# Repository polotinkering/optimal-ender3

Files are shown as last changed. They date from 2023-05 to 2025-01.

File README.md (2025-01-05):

# optimal-ender3
**the best ender 3 setup in my opinion !**
---
so here it is ! It's time to share the current setup of my printer . 
I think that i am currently running one of the best budget setup for an ender 3.
I have done these modification by necessity or some just for aesthetic but always on a budget (No micro swiss here^^)
---
So let's start :
I have organized my mods by letters :
- [1] :best mods practicaly essential in my opinion
- [2] :very useful
- [3] :usefull
- [4] :not essential (aesthetic mods)
---
**so here it is in all his glory:**
1684315006498 (1)

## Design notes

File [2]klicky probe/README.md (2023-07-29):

i have recently integrated the kevinakasam klack ender probe 

it's a very good adition to the solid silicon plots since it correct the warping of the bed and it's very cheap:  

you only need 6 magnets 4 screws and a microswitch .  

I will not do the complete guide here but if you want to try it here is the [klack ender github](https://github.com/kevinakasam/KlackEnder-Probe)


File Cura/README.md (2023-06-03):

This is my go to cura plofile for classic PLA print 
---
I also share the profile i use to print the parts of my future Voron V2.4 . (all voron recomanded settings)

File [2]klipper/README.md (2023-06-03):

Klipper
---
What an interesting modification !  
some will be surprised that i don't put it on [S] tier but i feel like you can have some really good results with the classic marlin firmware .
I want to adress a big thanks to [JSTECH](https://www.youtube.com/@Jstech3d) and all of his discord for the support and the help while setting up klipper .  
So I have used a raspberry pi 2b with the [fluidd](https://docs.fluidd.xyz/) interface .
I have struggle a lot during the setup of the wifi dongle so i share my mistakes to avoid you hours of troubleshooting:
- 1 wrong usb dongle .I was trying a 5v TP-link wifi dongle and the rapi only supply 3v .[here](https://elinux.org/RPi_USB_Wi-Fi_Adapters) is the list of compatibles dongles .
- 2 I was using a fluidd pi image instead of a classic os and it is not compatibles with external usb .[This video](https://www.youtube.com/watch?v=oM2kAnITNyE&t=190s) can be usefull for wifi setup.

So i went with a raspbian lite image that i have flashed through the [raspberry pi imager](https://www.raspberrypi.com/software/)on my sd card.  
After this I have put the sd card in the pi and connected it via SSH with [putty](https://www.putty.org/)
Now you can follow the [kiauh documentation](https://github.com/th33xitus/kiauh)it simply consist on pasting commands on the console .
you need to install :
- klipper 
- moonraker
- a web interface : mainsail or fluidd *I have choose fluidd*  

After you need a "printer.cfg" file i have shared mine in the files section of this folder .  

this is my interface:
fluidd

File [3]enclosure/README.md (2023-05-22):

simple ikea lack enclosure 
---
I have done it because im plannin gon building a voron andd for the voron i need a ABS capable machine .  
It's also very convinient because you can put things on top of the enclosure to keep more space on the desk .

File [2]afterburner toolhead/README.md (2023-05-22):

Voron afterbuner
---
one of the best upgrades i have done until now
this is why you would want to switch to afterbuner :
- print easily flexibles materials like TPU .
- do maintenance much more easily because it is very convenient to dissassemble .
- swap from one hot end to another realy quickly .
- have a much more slylish printer 😎.

I have reused the gear from my dual gear extruder seen above.  
it have worked perfectly great since the biggining and after swapping to a mosquito knock off i don't have any trouble when printing hight temp material like ABS or PETG.
And if you have a voron you can have a common stock of spare printed parts wich is realy convinient if you have a problem on one of your printers .  
Big thanks to the voron team for developping this toolhead !  
for this upgrade you will need :
- A [screw kit](https://fr.aliexpress.com/item/1005003998948585.html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) for afterburner because it's so much simple and not more expensive than self source all screw. aprox 10€
- 2040 24V [blower fan](https://fr.aliexpress.com/item/1005003879817745.html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) for about 4€.
- [dual gear kit](https://fr.aliexpress.com/item/1005005061611663.html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) (i have reused the one from my bond tech knock off)
- A [thiner stepper](https://fr.aliexpress.com/item/1005003226027617.html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) .15€  
Make sure to check the assembly manual before printing every thing .

Polish_20230518_120700527

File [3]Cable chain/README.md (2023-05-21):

Simple cable chain for the bed
it requiered :
- the printed parts 
- 2 or 4 zip ties


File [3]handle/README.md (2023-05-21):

Just a handle for easy carrying .
---
Print it pretty strong :
- 3 perimeters
- 20% infill or more
- 4 top/bottom  
files are from [this guy](https://www.thingiverse.com/guppyk/designs)


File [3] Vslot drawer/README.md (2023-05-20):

This is a simple 3d printed drawer for the included tools .  
You need:
- the printed part from [this guy](https://www.thingiverse.com/edison13/designs)
you can print it with your normal print setting with any filament .

drawer

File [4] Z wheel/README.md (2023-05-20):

this is a simple Z whell to move the Z axis easely.  
not that usefull but kinda cool !
---
it requiered :
- one printed part .from [this guy](https://www.thingiverse.com/s_vayner/designs)  
 


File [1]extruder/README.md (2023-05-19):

So first mod i have done to my ender 3 about 1 week after building the printer was changing the crappy plasticky extruder to a dual gear bondteck knock off :
---
this mod will cost you :
- about 15€ for [this very cheap knock off](https://fr.aliexpress.com/item/1005003423850142.html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)
- 30€ for [this good quality clone](https://fr.aliexpress.com/item/1005003092239261.html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)
- aproximately 100€ for [the original bontech](https://www.3djake.fr/bondtech/extruder-bmg-droit) depending from were you order

this mod is verry usefull and it will last you longer than the plastic one .
extrudr
*sorry for the bad photo quality i don't take photo of my printer too often*  

optionaly you can also like me upgrade later on the voron afterburner. *explenation on the afterbuner category*

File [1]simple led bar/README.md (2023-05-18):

This mod is pretty simple but in my opinion very usefull and it consist on a simple led strim on a holder in the top V slot .  
for this upgrade you will need:
- a simple [5v led strip](https://fr.aliexpress.com/item/1005003256544536.html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) it's 3€ for 1 meter (i power it from the bl touch port)*note:you can also power it from the psu with 24V leds*
- the 3 printed parts on the "STL" folder wich are from [this guys](https://www.thingiverse.com/smokyjoe/designs) (thanks to him) *note :you should print LED_Profile_V2.stl X2*
- some wire
- [A switch](https://fr.aliexpress.com/item/32822549892.html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) for around 3€ you can get 10 (I have choose a simple round one to make integration easier)
- maybe a connector if you want a clean instalation .


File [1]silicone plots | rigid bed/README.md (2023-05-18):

Silicon bed springs
---
In this page i will cover a very simple yet very usefull mod that i have done on day one :
these silicone plots instead of the original bed springs.  
It makes the bed a lot more rigid and don't require a lot of time and money so it's a must have on any I3 type of printer !
necessary parts :
- it will cost you around 4€ for [the kit of 4](https://fr.aliexpress.com/item/1005001823789355.html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) and are very durable


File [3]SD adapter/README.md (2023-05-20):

SD slot instead of micro SD
---
it's simple : micro sd is trash .  
It can't last very long ,it requiered more adapter to plug into your computer .
---
for this mod you will need :
- A [micro SD to SD adapter](https://fr.aliexpress.com/item/1005003299104936.html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) for about 3€ *make sure to select "TF-SD"*
- 2 printed parts
Polish_20230518_190414510
thanks to [Scott Yu-Jan](https://www.youtube.com/@ScottYuJan) for this remix and his videos

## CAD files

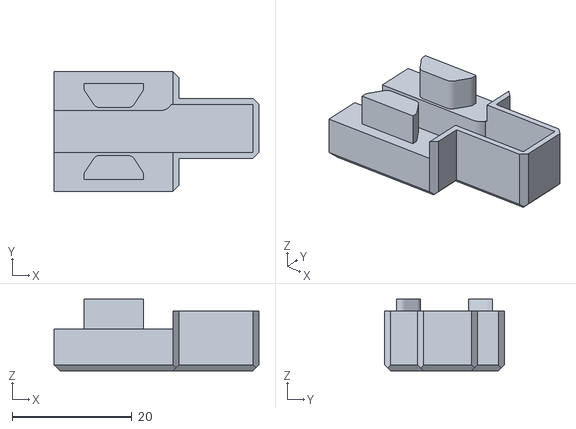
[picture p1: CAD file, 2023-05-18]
[1]simple led bar/STL/V2_V3_Endcap_left.stl
34.3 x 20.0 x 12.0

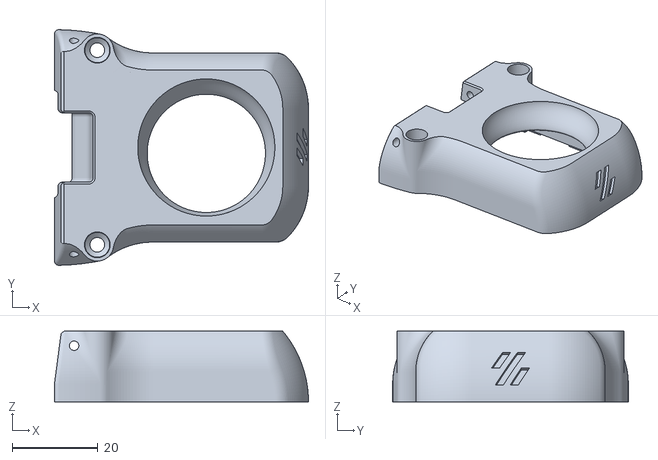
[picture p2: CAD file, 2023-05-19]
[2]afterburner toolhead/STL/Afterburner/[a]_blower_housing_front.stl
59.3 x 55.0 x 16.5

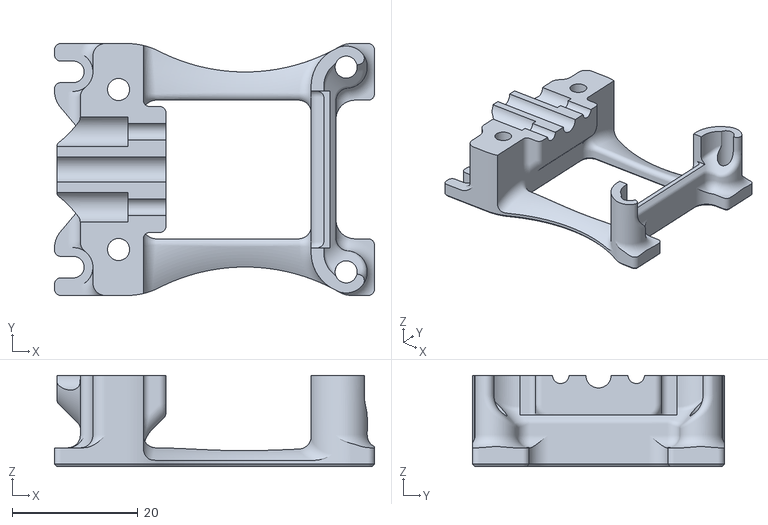
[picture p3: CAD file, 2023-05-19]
[2]afterburner toolhead/STL/toolcartridges/mosquito/printhead_rear_mosquito.stl
50.8 x 40.0 x 14.5

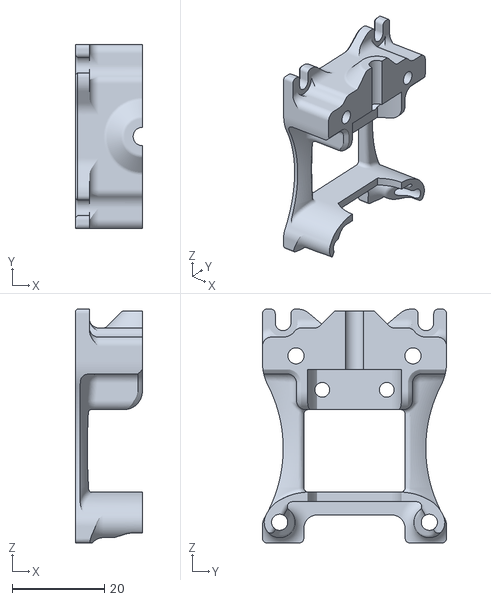
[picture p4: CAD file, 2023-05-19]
[2]afterburner toolhead/STL/toolcartridges/stock MK8/AB_Mk8_Ender5_stock_Back.stl
14.5 x 40.0 x 50.8

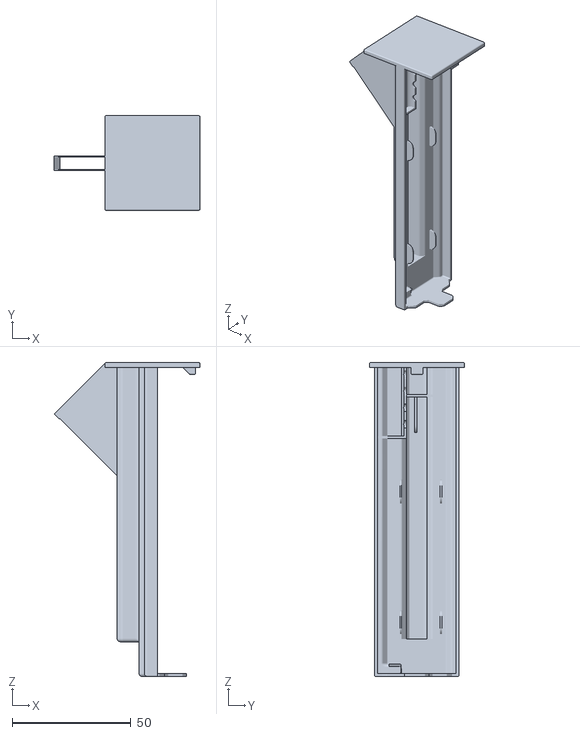
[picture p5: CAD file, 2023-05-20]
[3] Vslot drawer/STL/40x40AL_drawer_v3.STL
61.3 x 39.8 x 132.0

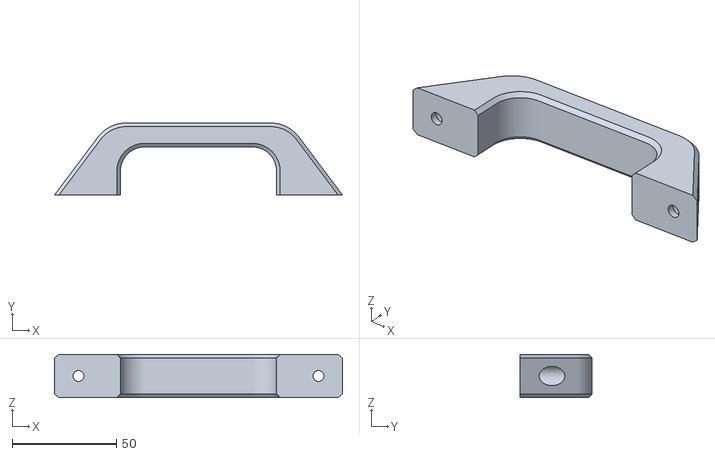
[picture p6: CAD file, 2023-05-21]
[3]handle/Handle_LARGE.stl
138.0 x 34.5 x 20.7

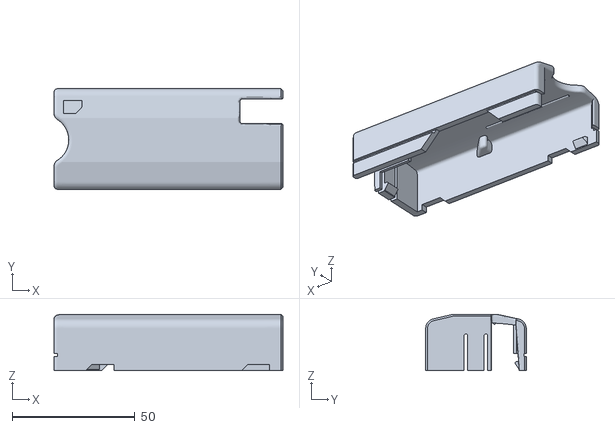
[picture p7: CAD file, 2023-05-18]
[3]SD adapter/STL/SD_Cover_remixed_updated_size.stl
93.4 x 41.0 x 23.0

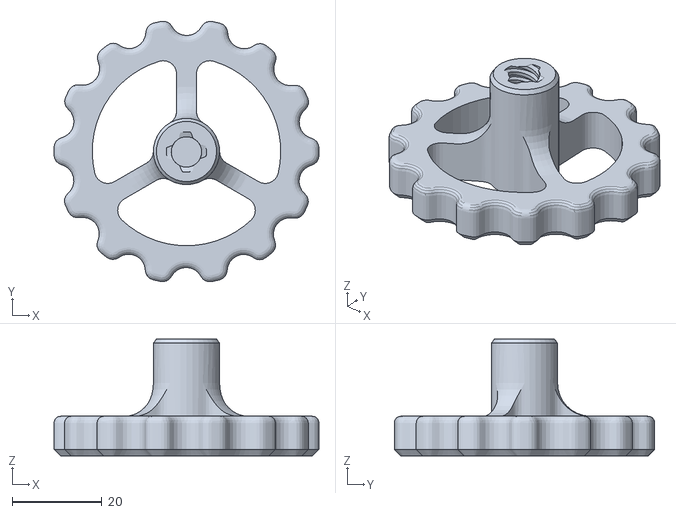
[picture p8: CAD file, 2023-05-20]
[4] Z wheel/STL/ZAxis_knob.stl
59.0 x 58.0 x 26.0

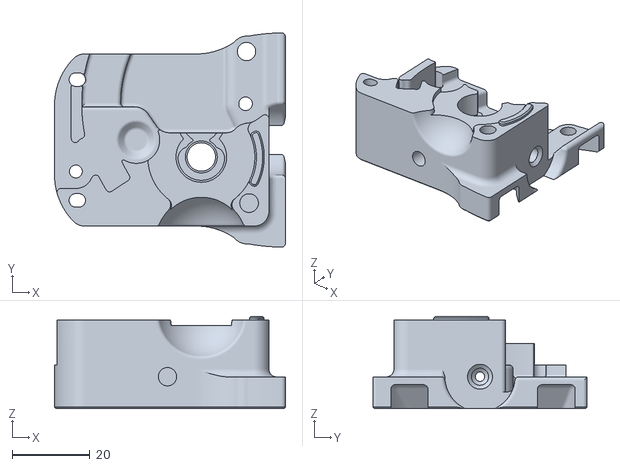
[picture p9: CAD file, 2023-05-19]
[2]afterburner toolhead/STL/Afterburner/extruder_body.stl
59.3 x 55.0 x 23.7

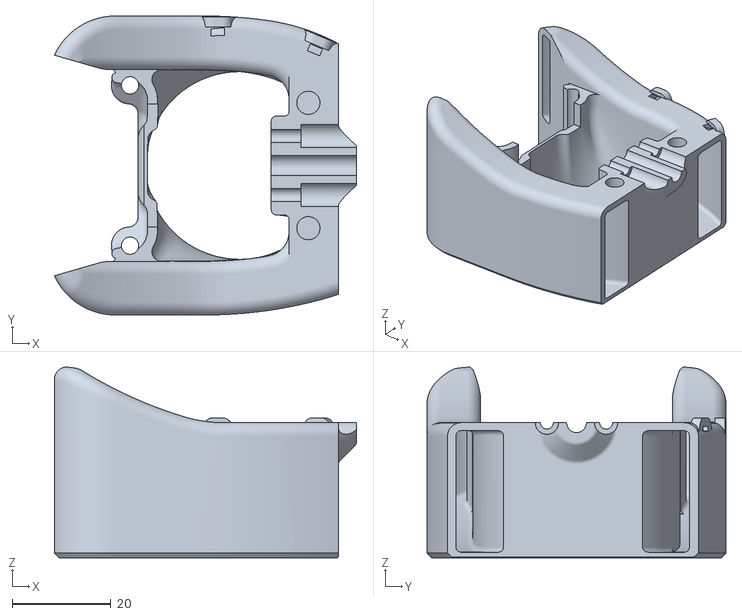
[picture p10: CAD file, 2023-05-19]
[2]afterburner toolhead/STL/toolcartridges/mosquito/printhead_front_mosquito.stl
61.2 x 60.6 x 38.7

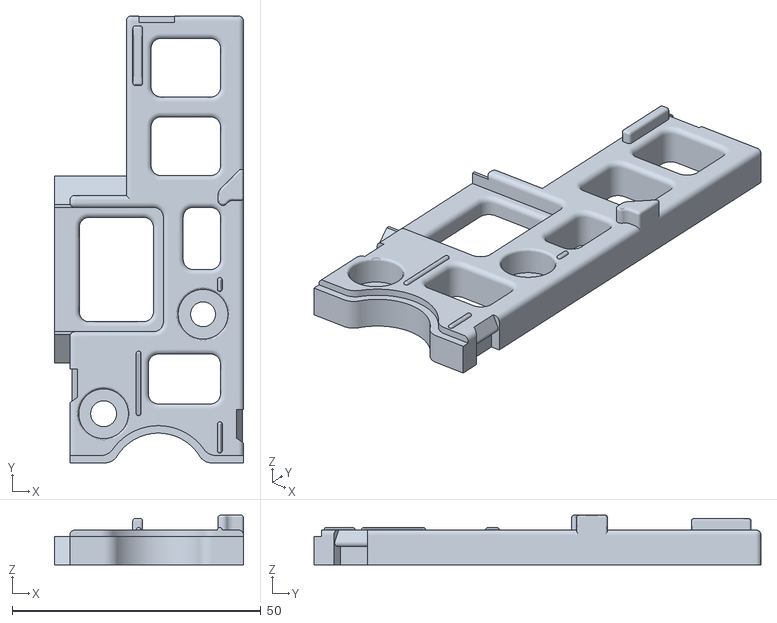
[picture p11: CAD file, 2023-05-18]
[3]SD adapter/STL/SD_base_plate .stl
38.0 x 89.9 x 10.00

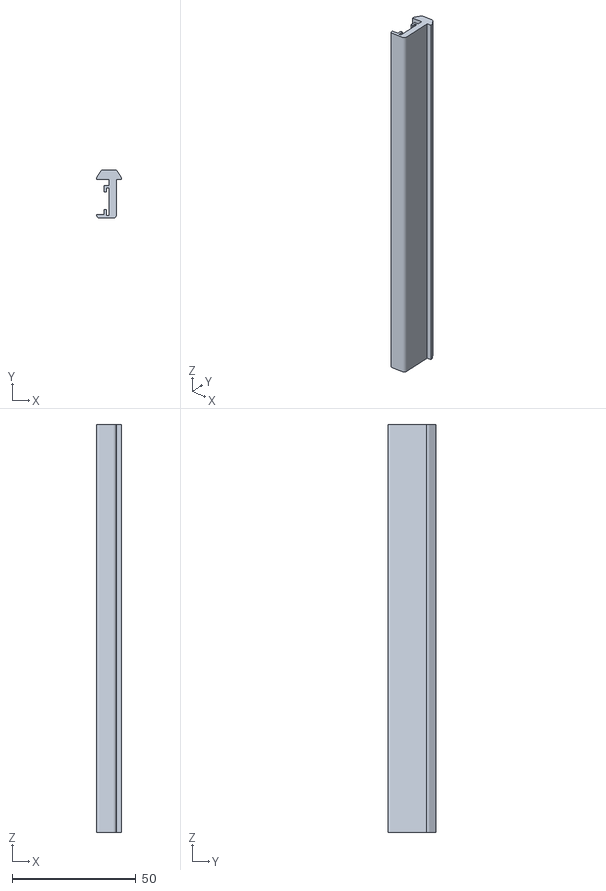
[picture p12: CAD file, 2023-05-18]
[1]simple led bar/STL/LED_Profile_V2.stl
10.0 x 19.6 x 165.0

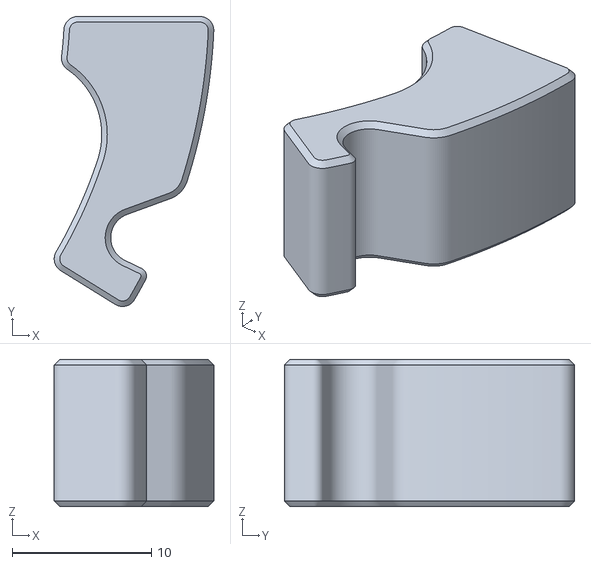
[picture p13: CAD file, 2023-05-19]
[2]afterburner toolhead/STL/Afterburner/[a]_latch_shuttle.stl
11.5 x 20.9 x 10.6

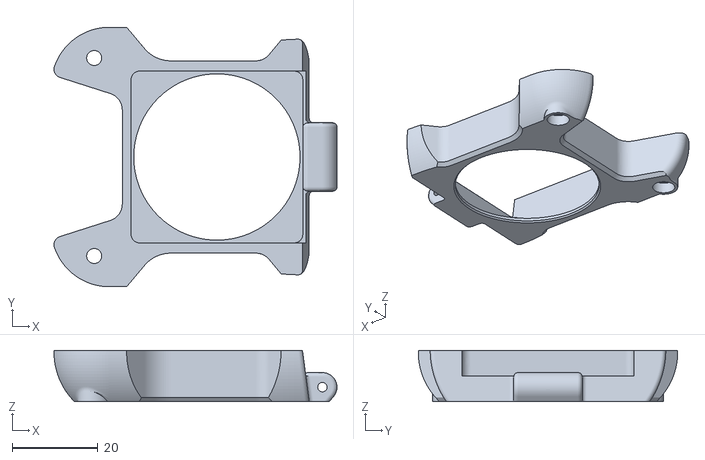
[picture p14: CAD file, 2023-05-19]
[2]afterburner toolhead/STL/Afterburner/hotend_fan_mount.stl
66.1 x 60.6 x 12.0

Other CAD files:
[1]simple led bar/STL/V2_V3_Endcap_right.stl
[2]afterburner toolhead/STL/Afterburner/[a]_latch.stl
[2]afterburner toolhead/STL/Afterburner/afterburner-motor-plate-ender3v2_BLT_updated.stl
[2]afterburner toolhead/STL/Afterburner/blower_housing_rear.stl
[2]afterburner toolhead/STL/Afterburner/[a]_guidler.stl

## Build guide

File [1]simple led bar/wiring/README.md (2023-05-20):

this is the wiring i used to power the leds :
---
wiring shema

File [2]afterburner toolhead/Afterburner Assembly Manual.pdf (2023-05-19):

1

# AFTERBURNER

### VORONDESIGN.COM

07-13-2021

2

CARRIAGE | VORONDESIGN.COM

M3x30 SHCS

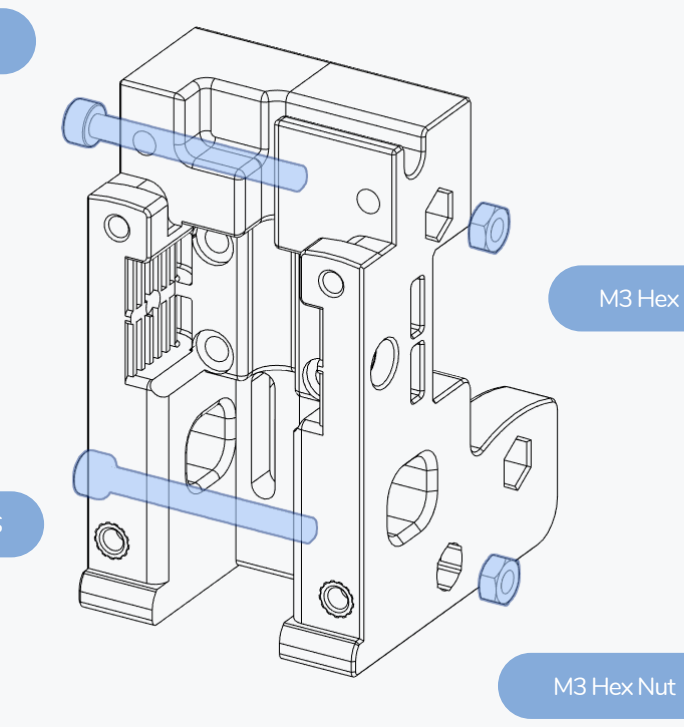
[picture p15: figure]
M3 Hex Nut

M3x30 SHCS

M3 Hex Nut

Heat Sets

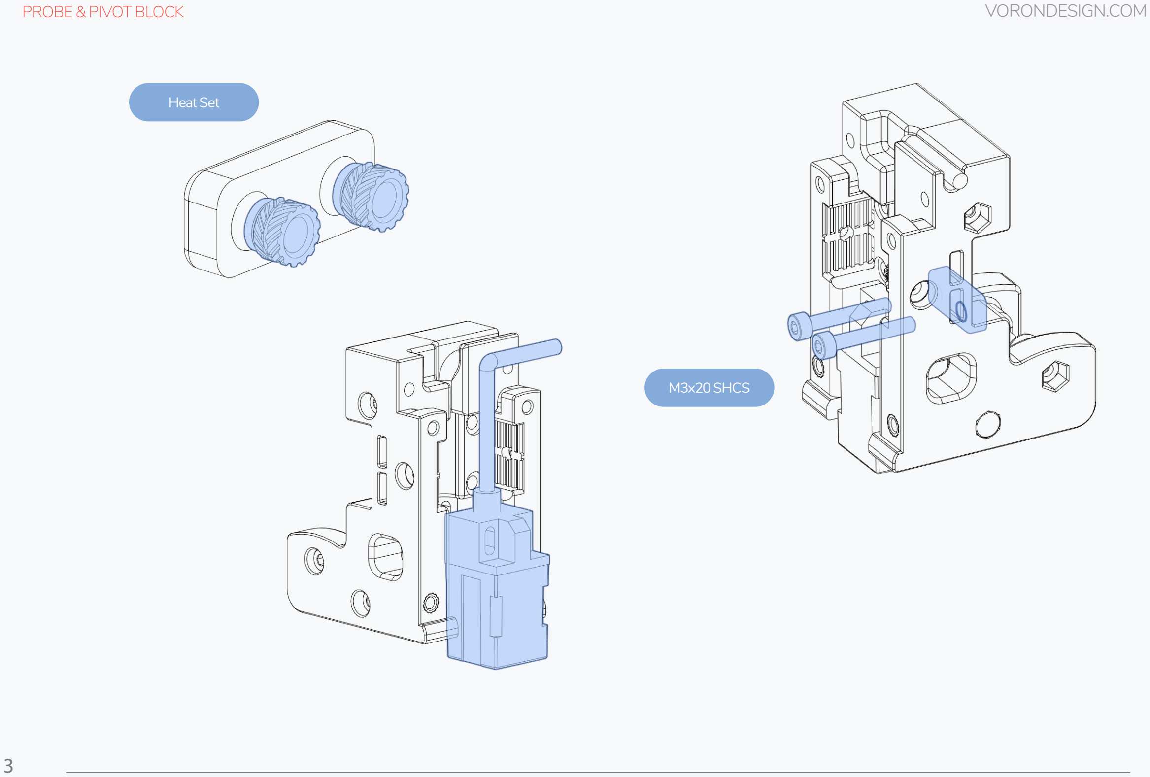
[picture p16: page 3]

3

PROBE & PIVOT BLOCK | VORONDESIGN.COM

Heat Set

M3x20 SHCS

4

XY BELT RETENTION | VORONDESIGN.COM

Heat Set

M3x12 SHCS

5

CARRIAGE MOUNTING | VORONDESIGN.COM

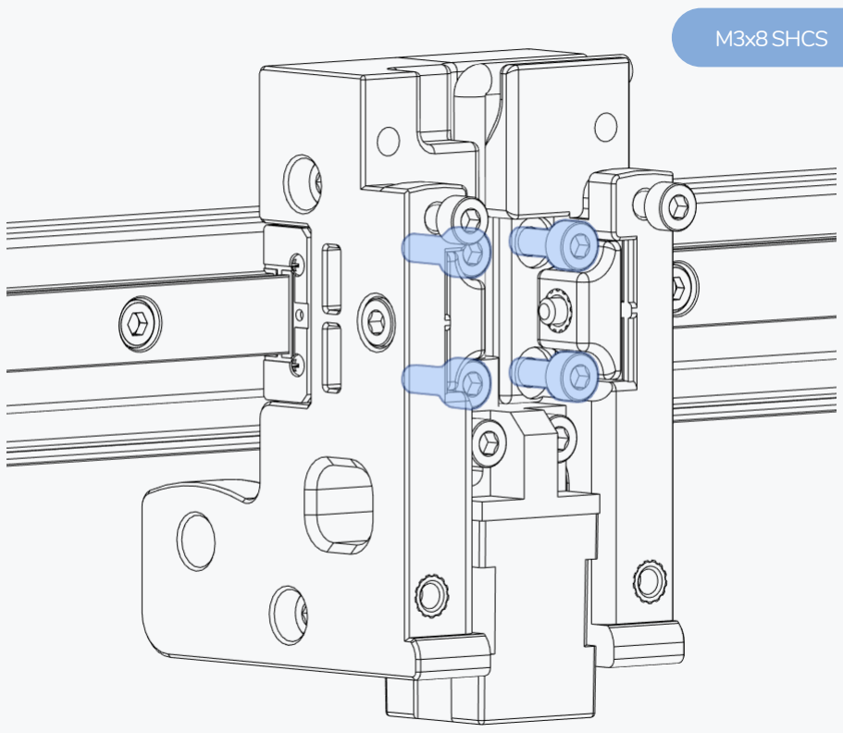
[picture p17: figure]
M3x8 SHCS

BUTTON HEAD OPTION
If you happen to have some M3x8 BHCS laying around
you can use those here. It can make belting the gantry in later steps a little easier but it’s not a big deal if you don’t have them.

PIVOT BLOCK | VORONDESIGN.COM

6

M3x8 SHCS
M3x30 SHCS

M3 Nut

DO NOT TIGHTEN (YET)
Leave these loose. You’ll need to aslign the rail before tightening. See discord if you need help with the correct procedure.

A BELT ROUTING | VORONDESIGN.COM

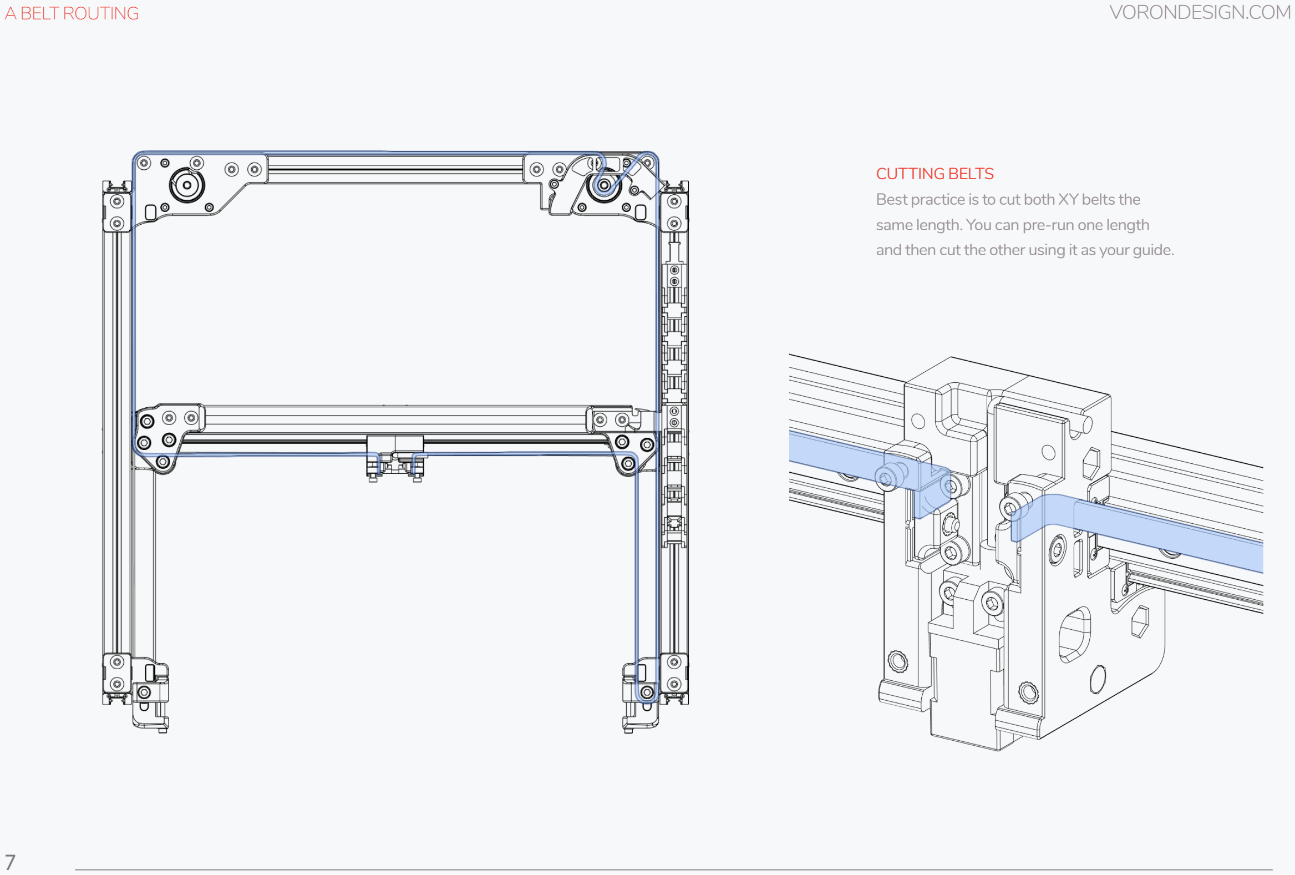
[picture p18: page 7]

7

CUTTING BELTS
Best practice is to cut both XY belts the same length. You can pre-run one length and then cut the other using it as your guide.

B BELT ROUTING | VORONDESIGN.COM

8

SECURING BELTS
Pick one side of the carriage and tighten the belts down flush with the front face. This allows you to pull the belts on the other side an equal length to help keep things square.

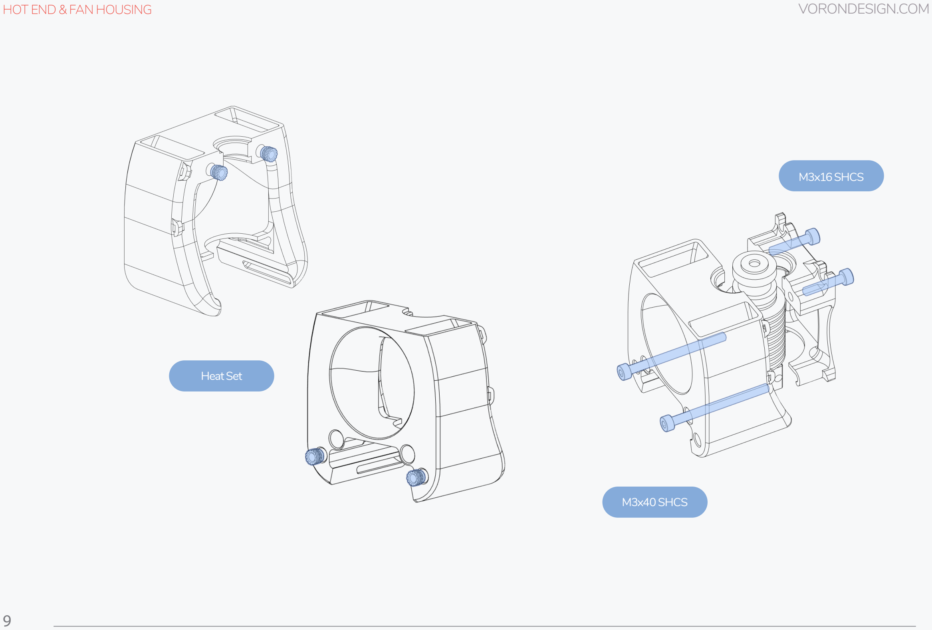
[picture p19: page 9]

9

HOT END & FAN HOUSING | VORONDESIGN.COM

Heat Set

M3x40 SHCS

M3x16 SHCS

10

HOT END RETENTION | VORONDESIGN.COM

M3x16 SHCS

TEST FIT HOUSING
Make sure to test fit the hot end housing. It should be able to slide in with firm pressure but not be loose enough that it can wobble.

11

CLOCKWORK HEAT SETS | VORONDESIGN.COM

INSTALL HEAT SET INSERTS
You will need to install heat set inserts into the locations shown on this page. Take note of the different cable chain mounts and use the one that best fits your build.

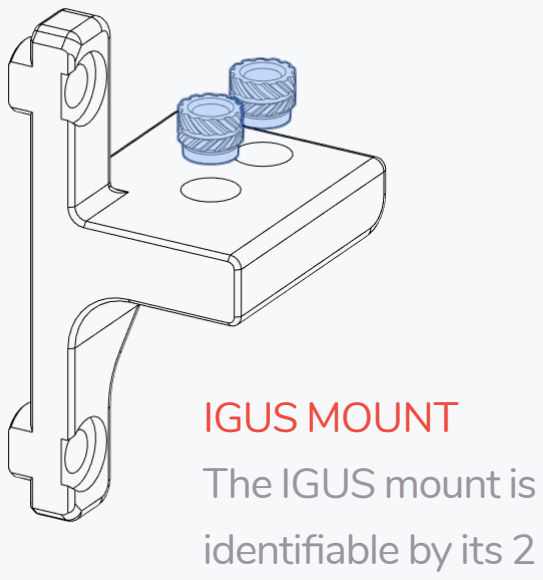
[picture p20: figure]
IGUS MOUNT The IGUS mount is identifiable by its 2
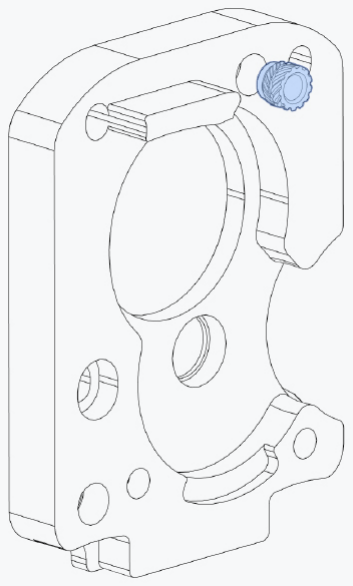
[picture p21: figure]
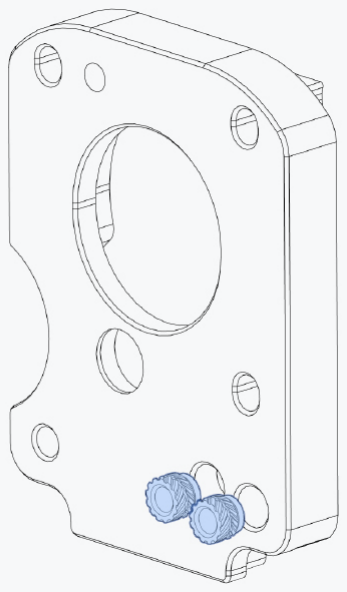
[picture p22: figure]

mounting holes.

is identifiable by its
3 mounting holes.

12

CLOCKWORK HEAT SETS CONT. | VORONDESIGN.COM

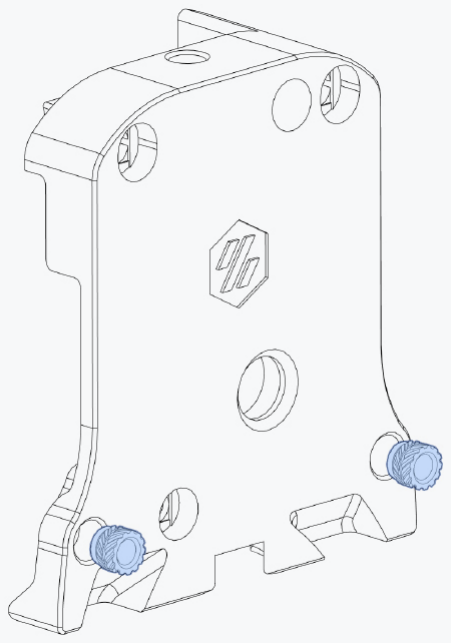
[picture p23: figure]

13

MOTOR PLATE | VORONDESIGN.COM

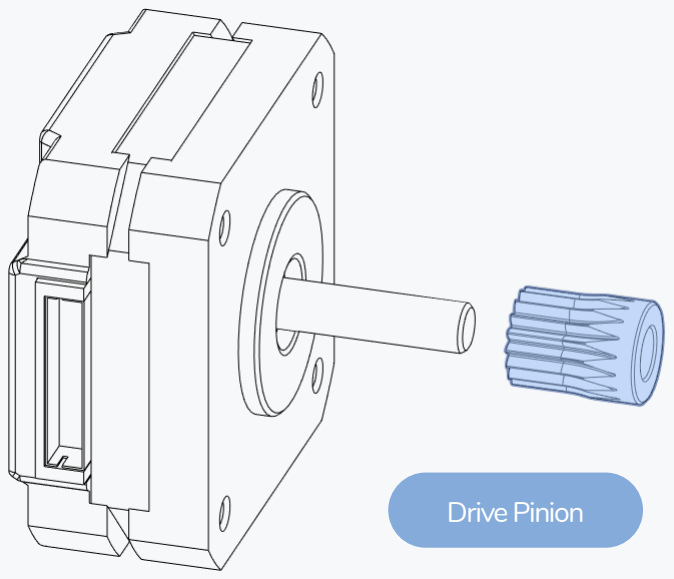
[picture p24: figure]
Drive Pinion
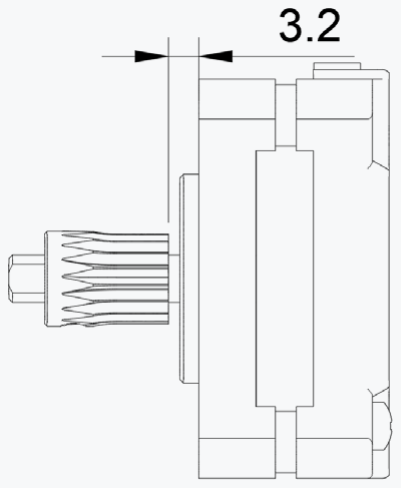
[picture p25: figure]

DRIVE PINION SPACING
Take care when installing the drive pinion on the extruder motor. It should be spaced 3.2mm from the main body of the stepper motor.

STEPPER MOTOR ORIENTATION
Make sure to orient the motor on the drive plate so that the wires are on the left side. This will allow correct routing through the cable cover that will be installed later.

14

MOTOR PLATE ALIGNMENT | VORONDESIGN.COM

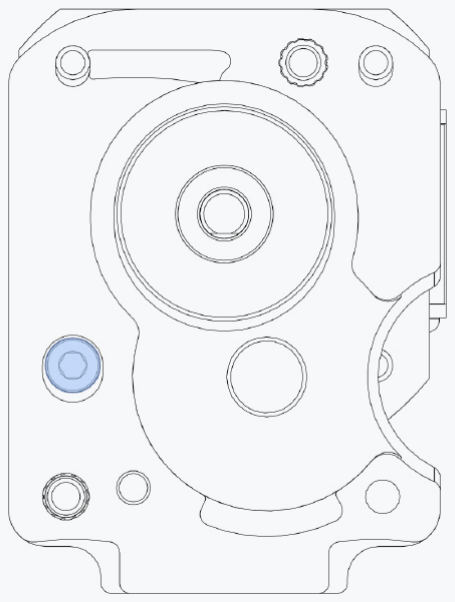
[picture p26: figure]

M3x8 SHCS

ADJUSTABLE MOTOR POSITION
The motor position is adjustable to allow for properly meshing of the drive gears.
We recommend you start in the top most position of the slot, but check Discord if you have questions on how to properly adjust this.

15

DRIVE GEAR | VORONDESIGN.COM

CHECK PLACEMENT
Ensure the filament drive gear is fully seated against the drive shaft gear.

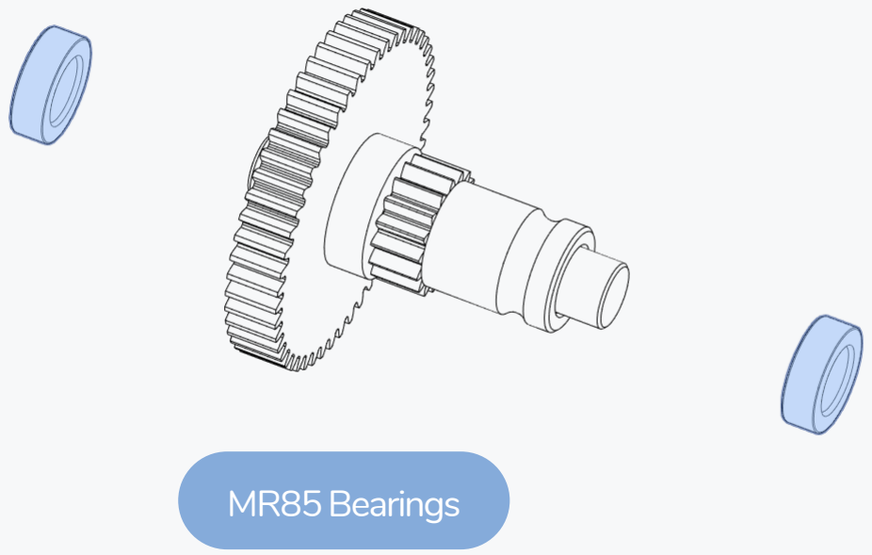
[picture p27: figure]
MR85 Bearings

BEARING FIT
The MR85 bearings should slip on to the drive shaft easily allowing the assembly to self center itself in relation to the filament.

If you find that they are too tight, you can lighty sand the drive shaft.

MAIN BODY | VORONDESIGN.COM

16

CHECK CLEARANCE
Make sure the drive shaft is not rubbing on the extruder motor. You can sand the face of the drive shaft if required.

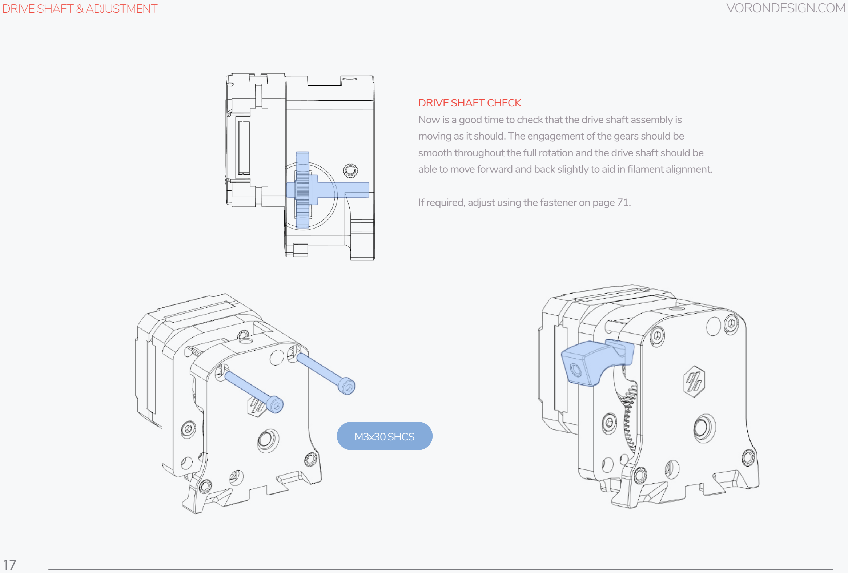
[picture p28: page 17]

17

DRIVE SHAFT & ADJUSTMENT | VORONDESIGN.COM

M3x30 SHCS

DRIVE SHAFT CHECK
Now is a good time to check that the drive shaft assembly is moving as it should. The engagement of the gears should be smooth throughout the full rotation and the drive shaft should be able to move forward and back slightly to aid in filament alignment.

If required, adjust using the fastener on page 71.

18

IDLER ASSEMBLY | VORONDESIGN.COM

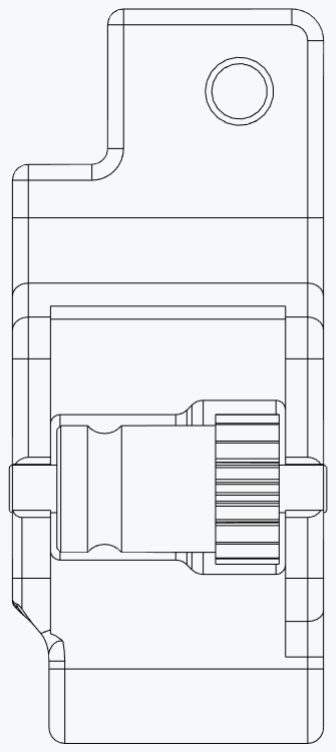
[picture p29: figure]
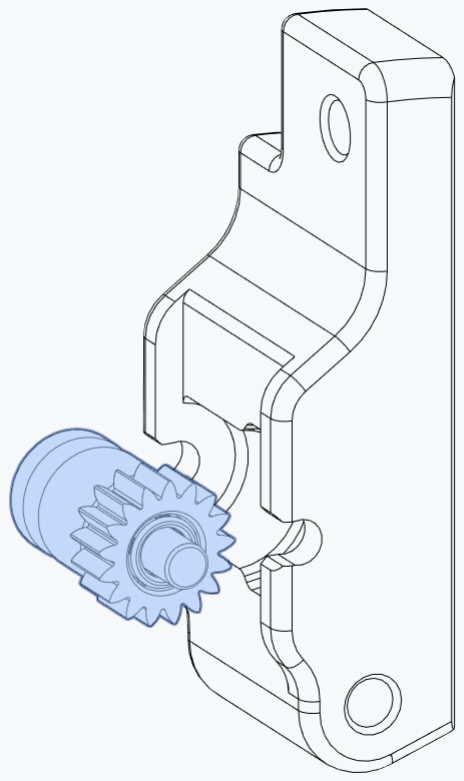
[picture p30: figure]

LUBRICATION
The idler assembly requires lubrication to ensure smooth operation and longevity. Refer to the BOM for lubricant options.

19

GUIDLER | VORONDESIGN.COM

M3x30 SHCS

20

LATCH INSTALL | VORONDESIGN.COM

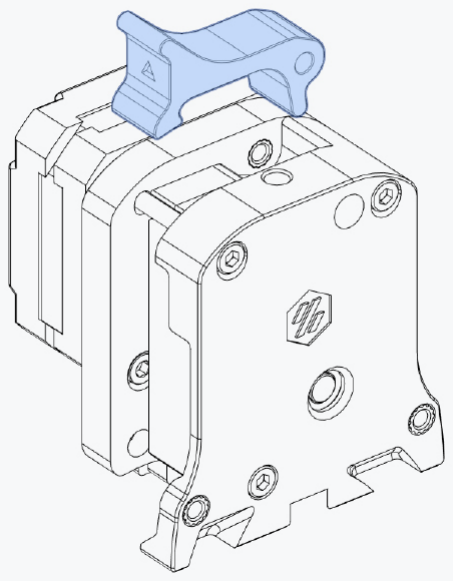
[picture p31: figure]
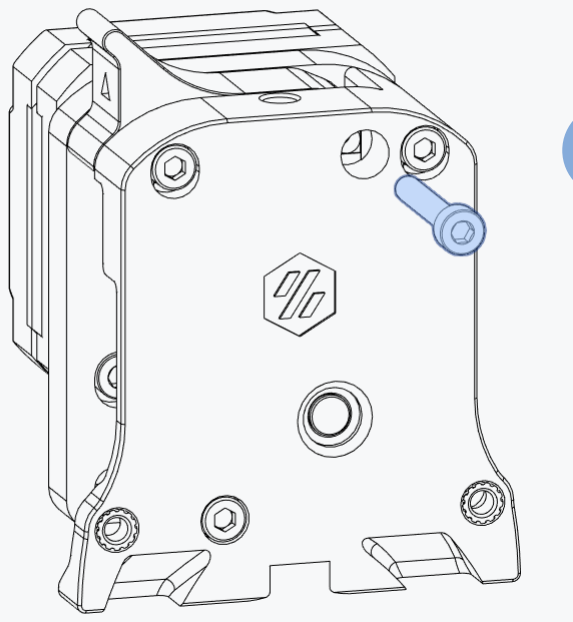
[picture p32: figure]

M3x20 SHCS

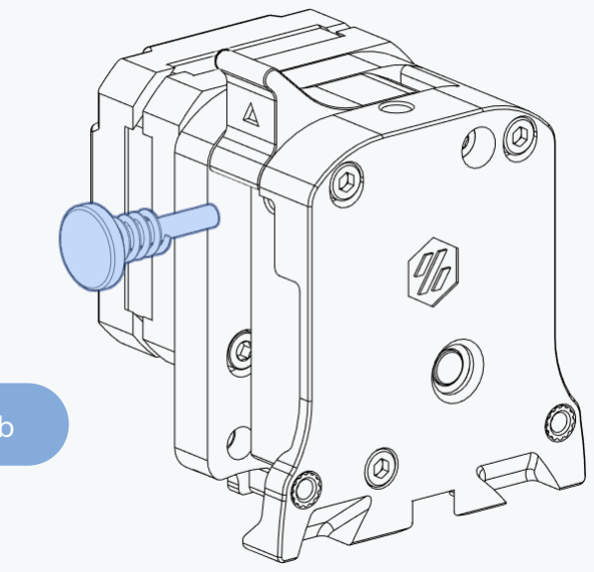
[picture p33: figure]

Tension Knob

21

CHAIN MOUNT | VORONDESIGN.COM

REMOVE SCREWS
Carefully remove the two screws on the left side of the extruder motor. We are going to be replacing these in further steps.

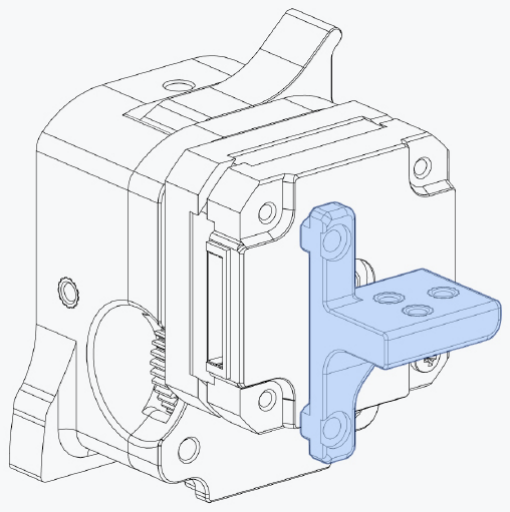
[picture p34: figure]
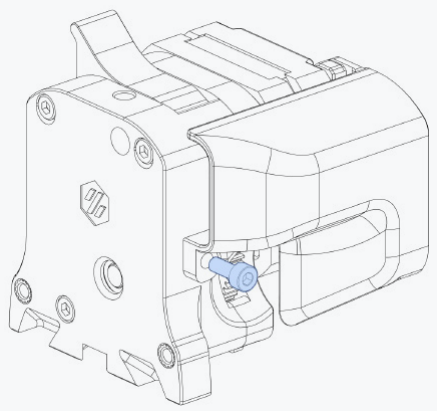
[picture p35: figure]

CABLE COVER | VORONDESIGN.COM

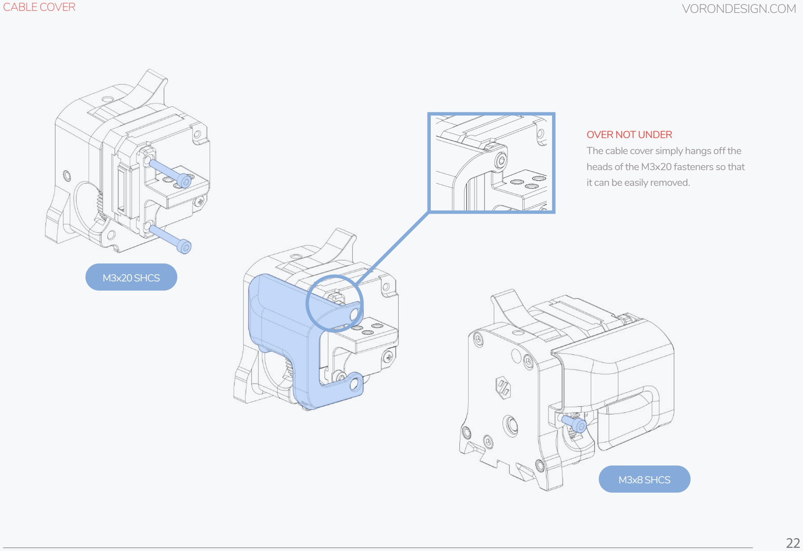
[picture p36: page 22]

22

M3x20 SHCS

M3x8 SHCS

OVER NOT UNDER
The cable cover simply hangs off the heads of the M3x20 fasteners so that it can be easily removed.

23

CLOCKWORK MOUNTING | VORONDESIGN.COM

M3x30 SHCS

M3x16 SHCS

M3x20 SHCS

M3x30 SHCS

HOT END INSTALL | VORONDESIGN.COM

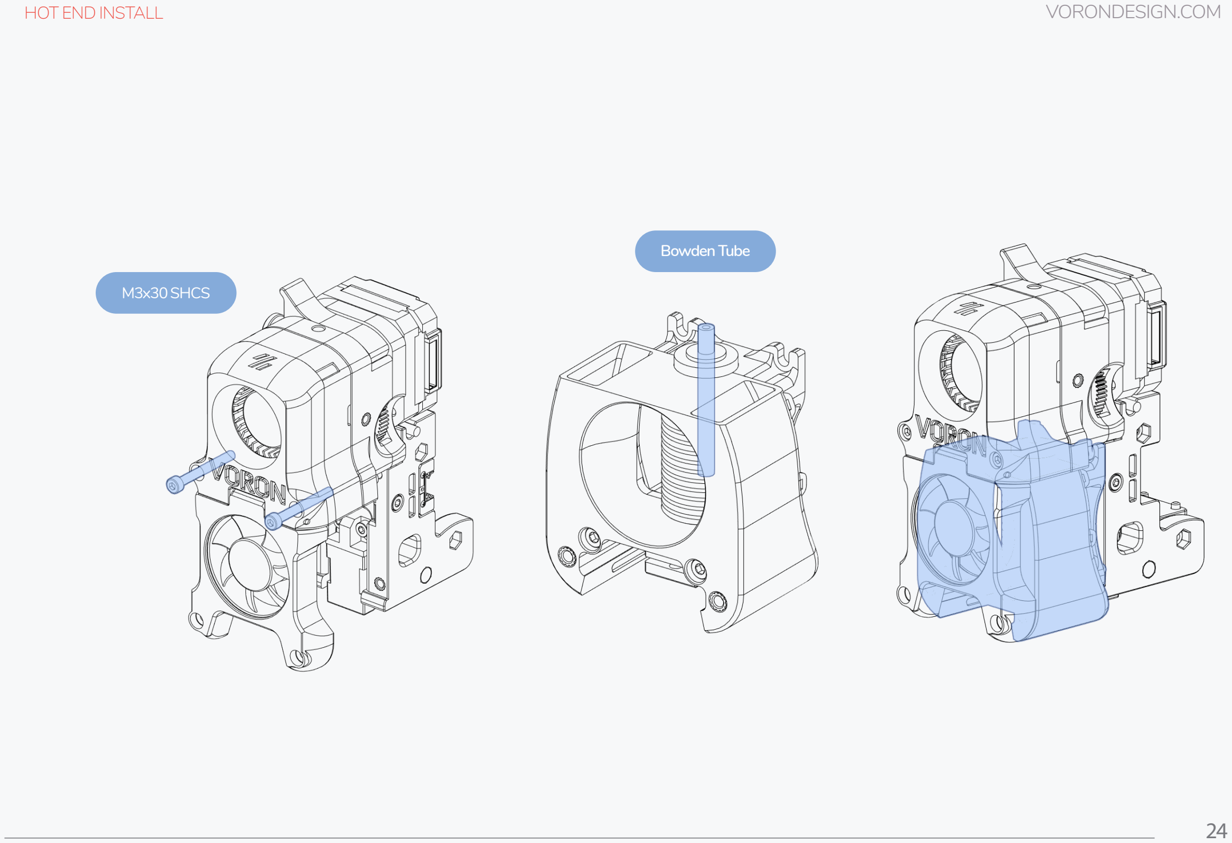
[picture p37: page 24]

24

Bowden Tube

M3x30 SHCS

HOT END INSTALL 2 | VORONDESIGN.COM

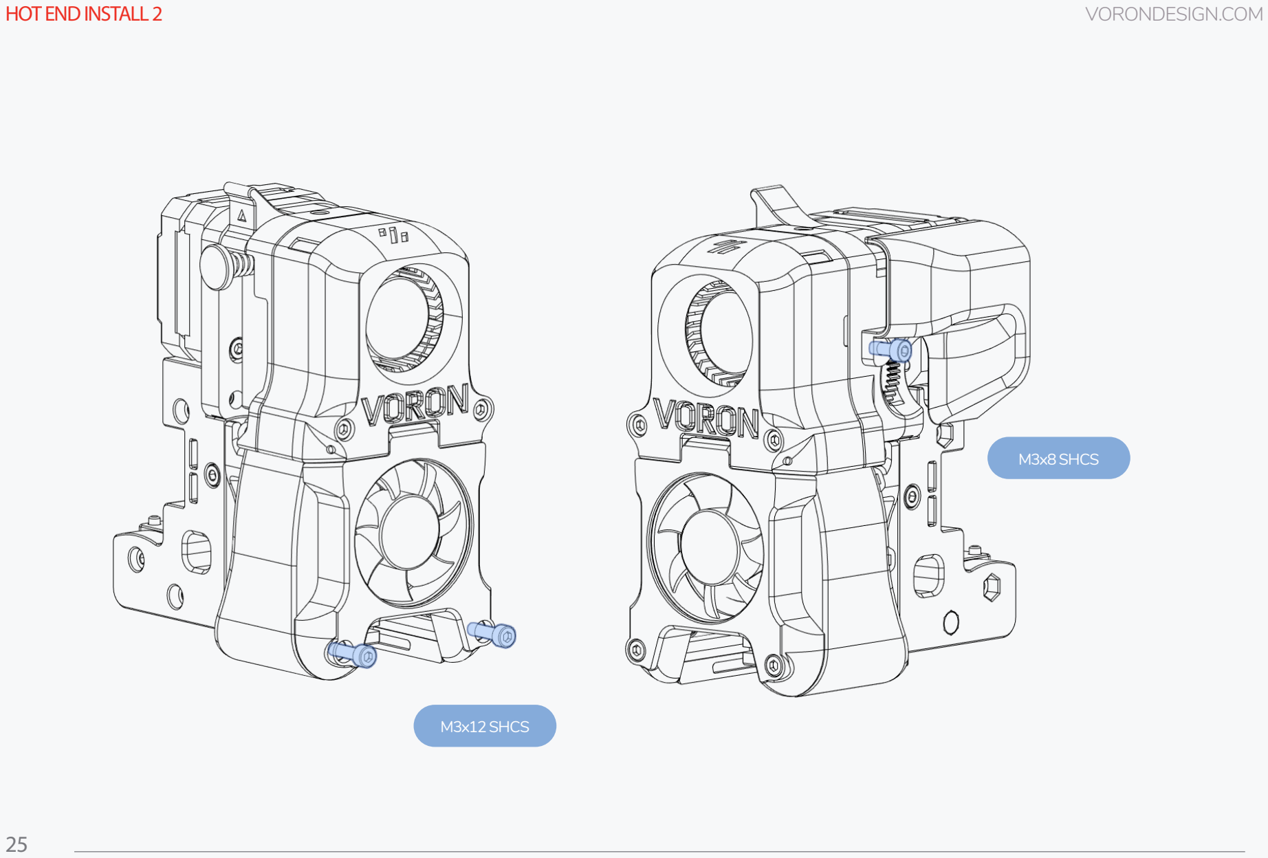
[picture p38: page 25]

25

M3x12 SHCS

M3x8 SHCS

26

### VORONDESIGN.COM

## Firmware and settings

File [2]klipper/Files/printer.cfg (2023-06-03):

# This file contains pin mappings for the stock 2020 Creality Ender 3
# V2. To use this config, during "make menuconfig" select the
# STM32F103 with a "28KiB bootloader" and serial (on USART1 PA10/PA9)
# communication.

# If you prefer a direct serial connection, in "make menuconfig"
# select "Enable extra low-level configuration options" and select
# serial (on USART3 PB11/PB10), which is broken out on the 10 pin IDC
# cable used for the LCD module as follows:
# 3: Tx, 4: Rx, 9: GND, 10: VCC

# Flash this firmware by copying "out/klipper.bin" to a SD card and
# turning on the printer with the card inserted. The firmware
# filename must end in ".bin" and must not match the last filename
# that was flashed.

# See docs/Config_Reference.md for a description of parameters.
[include preheat.cfg]
[include KlackEnderRev2.cfg]

[virtual_sdcard]
path: /home/pi/printer_data/gcodes

[mcu rpi]
serial: /tmp/klipper_host_mcu

[adxl345]
cs_pin: rpi:None

[resonance_tester]
accel_chip: adxl345
probe_points:
    100, 100, 30  # an example


[display_status]

[pause_resume]

[firmware_retraction]
retract_length: 2.0
retract_speed: 20
unretract_extra_length: 0
unretract_speed: 20

[stepper_x]
step_pin: PC2
dir_pin: PB9
enable_pin: !PC3
microsteps: 16
rotation_distance: 40
endstop_pin: ^PA5
position_endstop: -20
position_max: 235
position_min: -20
homing_speed: 50

[stepper_y]
step_pin: PB8
dir_pin: PB7
enable_pin: !PC3
microsteps: 16
rotation_distance: 40
endstop_pin: ^PA6
position_endstop: -12
#old setting "position_endstop: -12"
position_max: 235
position_min: -12
#old setting "position_min: -12"
homing_speed: 50

[stepper_z]
step_pin: PB6
dir_pin: !PB5
enable_pin: !PC3
microsteps: 16
rotation_distance: 8
endstop_pin: probe:z_virtual_endstop
#old endstop "endstop_pin: ^PA7"
#position_endstop: 0.0
position_max: 250
position_min: -2

[extruder]
pressure_advance = 0.1
max_extrude_only_distance: 800.0
max_extrude_cross_section: 50
step_pin: PB4
dir_pin: PB3
enable_pin: !PC3
microsteps: 16
rotation_distance: 7.3
nozzle_diameter: 0.400
filament_diameter: 1.750
heater_pin: PA1
sensor_type: EPCOS 100K B57560G104F
sensor_pin: PC5
control: pid
# tuned for stock hardware with 200 degree Celsius target
pid_Kp: 21.527
pid_Ki: 1.063
pid_Kd: 108.982
min_temp: 0
max_temp: 250

[heater_bed]
heater_pin: PA2
sensor_type: EPCOS 100K B57560G104F
sensor_pin: PC4
control: pid
# tuned for stock hardware with 50 degree Celsius target
pid_Kp: 54.027
pid_Ki: 0.770
pid_Kd: 948.182
min_temp: 0
max_temp: 130

[fan]
pin: PA0

[mcu]
serial: /dev/serial/by-id/usb-1a86_USB_Serial-if00-port0
restart_method: command

[printer]
kinematics: cartesian
max_velocity: 300
max_accel: 3000
max_z_velocity: 5
max_z_accel: 100

[gcode_macro PAUSE]
description: Pause the actual running print
rename_existing: PAUSE_BASE
# change this if you need more or less extrusion
variable_extrude: 1.0
gcode:
  ##### read E from pause macro #####
  {% set E = printer["gcode_macro PAUSE"].extrude|float %}
  ##### set park positon for x and y #####
  # default is your max posion from your printer.cfg
  {% set x_park = printer.toolhead.axis_maximum.x|float - 5.0 %}
  {% set y_park = printer.toolhead.axis_maximum.y|float - 5.0 %}
  ##### calculate save lift position #####
  {% set max_z = printer.toolhead.axis_maximum.z|float %}
  {% set act_z = printer.toolhead.position.z|float %}
  {% if act_z < (max_z - 2.0) %}
      {% set z_safe = 2.0 %}
  {% else %}
      {% set z_safe = max_z - act_z %}
  {% endif %}
  ##### end of definitions #####
  PAUSE_BASE
  G91
  {% if printer.extruder.can_extrude|lower == 'true' %}
    G1 E-{E} F2100
  {% else %}
    {action_respond_info("Extruder not hot enough")}
  {% endif %}
  {% if "xyz" in printer.toolhead.homed_axes %}
    G1 Z{z_safe} F900
    G90
    G1 X{x_park} Y{y_park} F6000
  {% else %}
    {action_respond_info("Printer not homed")}
  {% endif %} 



[gcode_macro RESUME]
description: Resume the actual running print
rename_existing: RESUME_BASE
gcode:
  ##### read E from pause macro #####
  {% set E = printer["gcode_macro PAUSE"].extrude|float %}
  #### get VELOCITY parameter if specified ####
  {% if 'VELOCITY' in params|upper %}
    {% set get_params = ('VELOCITY=' + params.VELOCITY)  %}
  {%else %}
    {% set get_params = "" %}
  {% endif %}
  ##### end of definitions #####
  {% if printer.extruder.can_extrude|lower == 'true' %}
    G91
    G1 E{E} F2100
  {% else %}
    {action_respond_info("Extruder not hot enough")}
  {% endif %}  
  RESUME_BASE {get_params}


[gcode_macro CANCEL_PRINT]
description: Cancel the actual running print
rename_existing: CANCEL_PRINT_BASE
gcode:
  TURN_OFF_HEATERS
  CANCEL_PRINT_BASE
  G28 X
  M106 S0


[gcode_macro START_PRINT]
gcode:
    # Reset the G-Code Z offset (adjust Z offset if needed)
    G28
    PURGE



[gcode_macro END_PRINT]
gcode:
    # Turn off bed, extruder, and fan
    M140 S0
    M104 S0
    M106 S0
    # Move nozzle away from print while retracting
    G91
    G1 X-2 Y-2 E-3 F300
    # Raise nozzle by 10mm
    G1 Z10 F3000
    G90
    G28 X
    # Disable steppers
    M84



[gcode_macro PURGE]
gcode:
    G28
    G1 X20 Y20 F3000 
    G92 E0 
    G1 Z0.4
    G1 X55 E50 F225 
    G1 X75 Y20 F2100
    G92 E0


[input_shaper]
#shaper_type_x = 3hump_ei
#shaper_freq_x = 116.8
shaper_type_y: mzv
shaper_freq_y: 33.2

#*# <---------------------- SAVE_CONFIG ---------------------->
#*# DO NOT EDIT THIS BLOCK OR BELOW. The contents are auto-generated.
#*#
#*# [bed_mesh default]
#*# version = 1
#*# points =
#*# 	  -0.006250, 0.023750, 0.402500, 0.790000
#*# 	  -0.026250, 0.065000, 0.412500, 0.675000
#*# 	  -0.072500, -0.027500, 0.266250, 0.417500
#*# 	  -0.100000, -0.050000, 0.206250, 0.000000
#*# x_count = 4
#*# y_count = 4
#*# mesh_x_pps = 4
#*# mesh_y_pps = 4
#*# algo = bicubic
#*# tension = 0.2
#*# min_x = 8.0
#*# max_x = 222.97
#*# min_y = 30.0
#*# max_y = 201.0
#*#
#*# [input_shaper]
#*# shaper_type_x = ei
#*# shaper_freq_x = 92.6

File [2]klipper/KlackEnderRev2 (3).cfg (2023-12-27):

##################
## BETA VERSION ##
##################

########################
## Basic instructions ##
########################

#With this config you will set the probe as your z endstop. This makes the initial setup a bit more tricky than with the Rev1.
#The printer will set you bed position as Z0 (because it probes on that).
#You have to roughtly position the Probe_Retainer for the first setup before you can set the final position. The !top! of the arm has to be roughtly 1mm above the bed.
#To find the perfect position of the Probe_Retainer you have to home the z axis. After this the probe will be at the new Z0 position.
#Place the Probe_Retainer close to the block so there's just a small gap between them.

##Attention!##
#Youre using the Probe as your Z endstop. This means that the position Z0 is also affected by your Z offset.
#Keeep that in mind when positioning the Probe_Retainer
#You might have to change the position of the Probe_Retainer after you set your z offset (0.x mm changes wouldn't changes that much but for everything >1mm you should check its positioning).
#And a kindly reminder to adapt the [probe] pin, set the virtual endstop, set the y min posistion.

##################################
## Add this to your printer.cfg ##
################################## 
#####################################################################
#	KlackEnder- Settings
#####################################################################

# !! Change your Z endstop pin from 'endstop_pin: Pin123' to 'endstop_pin: probe:z_virtual_endstop'
# !! Also add in [stepper_y] 'position_min: -8'. Idk why but most configs mave this wrong. For the Stock Ender 3 the homed Y position is -8.

[probe]
pin: ^PA7 #Probe-Stop Connection on creality 4.2.7
z_offset: 7.549 #Measure per your specific setup
x_offset: 22 # negative = left of the nozzle
y_offset: 37 # negative = in front of of the nozzle
speed: 5.0
lift_speed: 15.0
sample_retract_dist: 1
samples: 2
samples_tolerance_retries: 6

##[(7x7)-1] / 2 = 24
##[(5x5)-1] / 2 = 12
[bed_mesh]
speed: 500
horizontal_move_z: 7
mesh_min: 8,30
mesh_max: 223,201
probe_count: 4,4
algorithm: bicubic
fade_start: 1
fade_end: 10
#fade_target:
#   The z position in which fade should converge. When this value is set
#   to a non-zero value it must be within the range of z-values in the mesh.
#   Users that wish to converge to the z homing position should set this to 0.
#   Default is the average z value of the mesh.
split_delta_z: 0.015
#   The amount of Z difference (in mm) along a move that will
#   trigger a split. Default is .025.
move_check_distance: 3
#   The distance (in mm) along a move to check for split_delta_z.
#   This is also the minimum length that a move can be split. Default
#   is 5.0.
mesh_pps: 4,4
#   A comma separated pair of integers (X,Y) defining the number of
#   points per segment to interpolate in the mesh along each axis. A
#   "segment" can be defined as the space between each probed
#   point. The user may enter a single value which will be applied
#   to both axes.  Default is 2,2.
#bicubic_tension: .2
#   When using the bicubic algorithm the tension parameter above
#   may be applied to change the amount of slope interpolated.
#   Larger numbers will increase the amount of slope, which
#   results in more curvature in the mesh. Default is .2.

[homing_override]
axes:Z
set_position_z:0 # Make printer think Z axis is at zero, so we can force a move upwards away from build plate
gcode:
    G90
    G1 Z10 F3000 ; move up to prevent accidentally scratching build plate    
    G28 X
    G28 Y
    PROBE_OUT
    G1 X117 Y117 F6000
    G28 Z
    PROBE_IN


#####################################################################
#	KlackEnder- Macros
#####################################################################

[gcode_macro PROBE_OUT]
gcode:
    G90
    G1 X225 F4000
    G4 P300
    G1 Z15
    G1 X0

[gcode_macro PROBE_IN]
gcode:
    G90
    G1 Z20
    G1 X225 F20000
    G1 Y-8
    G1 Z0
    G4 P300
    G1 X215 F6000
    G1 Z10
    G1 X0

[gcode_macro AUTO_BED_MESH]
gcode:
    PROBE_OUT
    BED_MESH_CALIBRATE
    #G1 Y0 F20000
    PROBE_IN

[gcode_macro G29]
gcode:
    PROBE_OUT
    BED_MESH_CALIBRATE
    #G1 Y0 F20000
    PROBE_IN

[gcode_macro Accuracy_Test]
gcode:
    PROBE_OUT
    G90
    G1 Y120 X120 F20000
    PROBE_ACCURACY
    PROBE_IN

[gcode_macro AUTO_Z_TILT_ADJUST]
gcode:
    PROBE_OUT
    Z_TILT_ADJUST
    PROBE_IN
